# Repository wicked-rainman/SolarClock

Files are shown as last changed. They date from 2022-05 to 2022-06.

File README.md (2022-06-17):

# SolarClock
<p align="center">
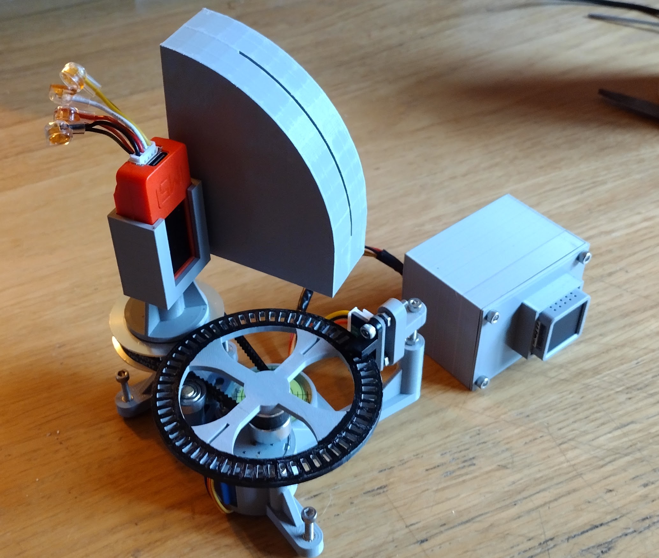
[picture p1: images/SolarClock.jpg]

</p>
 
This project shouldn't be confused with a plan to design a clock powered by solar energy. That's not what this is about. Instead, it represents an academic attempt at calculating the time based on the position of the sun in the sky.

Yes, you could look at your watch, listen for the pips on the radio or even glance at your mobile phone - but this isn't a move to try and replace those reliable sources. It's more about trying to observe the local environment and making calculations around what can be seen.   

I can't pretend when this is finished it will have much value - it's more of a nonsense machine bred out of boredom. Regardless, I do think it will be interesting to see how accurately time can be calculated using a bunch of cheap electronics and some 3D printed tat.
 
There will probably end up being just two main components in all of this:

- A "Stepper motor server" being driven via an M5Atom-matrix, although any esp32/Arduino type platform would do. I chose the Matrix because I had one spare and could make use of the LED array for added glitz.
- A "Stepper client" that will read light values and instruct the server how far to rotate after each reading. This component is based round an M5Stick because it's got a built in battery that helps negate the need for trailing wires being dragged round by the rotating platform.

When I started out on this venture, I tried using an I2C based compass (LSM303) for azimuth alignment. Like any "sundial", you have to know which way is north. The LSM303 claimed a 0.1 degree resolution, but after some failed tests and a bit of reading I discovered that although the resolution is good, accuracy is +-5 degrees. Given that the earth rotates through roughly 15 degrees in an hour, It just wouldn't provide the accuracy I'm looking for. So, in the end I went back to the drawing board and came up with a timing disk design. The main drawback of this approach is you need to manually ensure the light sensing unit is facing true north whenever you press the inevitable "go" button. This dosen't satisfy me as a solution, but for now it will have to do.

## North
Finding true north is problematic. You could use a normal magnetic compass and deal with the offset, but from what research I've done so far this seems a little vague (Magnetic north is always on the move). I'm still considering adding some form of gnomon to the rotator base so it can be aligned (after performing solar observations), but that loses the semi-instant gratification of just pushing a button I've also been considering a gyro, but that leads towards the chicken and egg situation of still not actually knowing where true north is in the first place. I've read some of the physics and I'm well aware that a gyro can achieve this because it's affected by the rotation of the earth. Such a gyro is really expensive and I don't think I'm capable of constructing one of my own. For now I'm going to carry on testing commercially availble magnetometers to see if there's something better than the LSM303. Watch this space.

<b><i>Updates:</i></b>

- 12th June 2022. Finished an evaluation of another magnetometer, the BMM150. I chose this one to test because it's actually sold as a viable and accurate compass. In my usecase, this still proved to be unreliable. I have a suspicion that even after calibration the environment is too electrically noisy. I'm currently planning to drop the idea of using any of these i2c devices, although I might change my mind at a later stage. I'm now thinking there may need to be a physically separate component to this project in order to perform the initial allignment. 

- Going back to the drawing board again, I've since discovered that for my geographic area, the magnetic declination is currently 0.12 mins, i.e. 0.2 degrees. I don't know what the annual variation is, but I'm heading towards the more simple concept of just drawing an accurate east/west line. I'll position the rotating head at a right angles to this before I start. I can draw the rhumb line "offline" so there is no equipment interference and for now, just accept the accuracy of a normal bearing compass. 

<p align="center">
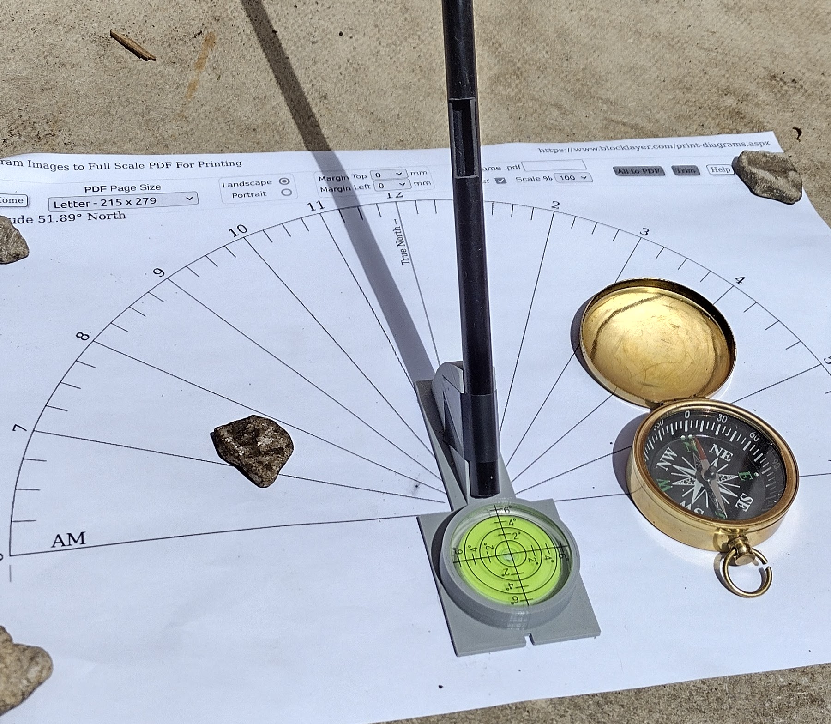
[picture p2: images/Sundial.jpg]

</p>

- Performed some cross check tests in the back garden to correlate the whole magnetic north/true north solar time theory. I don't know why, but I'm surprised at just how accurate the results are. This gives me some confidence that I should be able to correctly calculate the time within at least a 15 min window. Clearly, my earlier views were just plain wrong! 

## The Components - Stepper motor server

- M5Atom matrix (*The Stepper motor WiFi server platform*)
- 28BYJ-48 5V stepper motor with ULN2003 driver
- Infra-red photo interrupter sensor
- Round button-type spirit level
- GT2 200 tooth belt, 20 and 60 tooth belt pulley
- 5mm brass rod
- Pulley tensioner bearing (*14mm od, 5mm id*)
- 3d M3 inserts (12)
- Assortment of M3 machine screws
- 3D printed components - as stored in the STL directory
- (Maybe a desire to wait for a day when it isn't raining and you can see the sun?)

## Stepper client

- M5Stickc (I'm using the PLUS variant)
- BH1750 light sensor (*in I2C mode*)
- Some (as yet to be decided) magnetometer

## Notes:

- This is a work in progress !!
- In the UK, the sun can rise at 50 degrees east and set at 310 west (this is it's local maximum azimuth boundary). The stepper motor client has therefore been set to only sweep between these angles, one degree (but 30 odd stepper motor half steps) at a time. In theory, this should allow for a resolution of about 2 mins, but I doubt that such accuracy is achievable.
- The HM1750 light sensor on the client has been set up so it only has a 1mm vertical view of the sky (from an elevation of 10 degrees through to 65 - the minimum and maximum throughout the year. The container box for the sensor looks odd, but there is a reason behind this. Obviously, the closer the sensor is to the apeture, the more of the sky can be seen (Think peeping through a keyhole). Given that the stepper platform is being advanced by one degree at a time, it seemed to make sense for the sensor view to be similarly restricted. I have no idea if this is the right decision, but it's only another 3d print away from being correctable!. In theory, 360mm circle circumference means a 57.3mm viewing radius - thus the odd size and shape.  
- The pulley ratio on the stepper server is 3:1 - I.E, the stepper motor has to rotate three times in order for the output pulley (the base) to rotate once. The timing disc has 60 slots in it - giving 120 pulses (60 on and 60 off) per revolution. 120 x 3 = 360. The stepper motor seems to take 40 odd half steps to clear a slot and roughly 20 to clear each space. Part of the reason for this difference is that the top edges of the space segments are narrower than the bottom. Using Tinkercad I couldn't see a way round this issue - but I don't believe it's going to matter that much. If it does become problematic the difference can be catered for in the code.  

<p align="center">
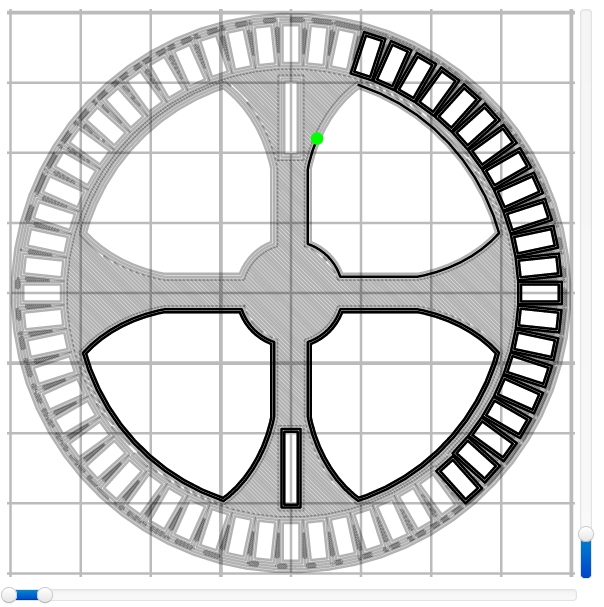
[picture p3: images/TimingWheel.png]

</p>
 <p align="center">
 <b>The mark and space variation</b>
</p>

- The Stepper client and server communicate over WiFi using UDP. What with the M5Stick's built in battery this removes any need for wiring between the stepper base and rotator. I decided on UDP rather than TCP to reduce cpu loads. Communication re-tries are seen, but the current code seems to address this shortfall.

```mermaid
sequenceDiagram
    participant StepperClient
    participant StepperServer
    participant UDPBroadcast
    Note left of StepperClient: Press M5Stick<BR/> Button A.
    StepperClient->>StepperServer: Rotate request for 50 North, UDP port 5001
    StepperServer->>StepperClient: Ack on UDP port 5002, now pointing 50 North
    activate StepperClient
    Note left of StepperClient: Repeat in 1 degree<br>increments until<BR/>310 degrees reached.
    StepperClient->>StepperServer: Rotate request for 1 degree clockwiseff (UDP port 5001)
    StepperServer->>StepperClient: Rotate 1 degree Ack, (UDP 5002)
    StepperClient->>UDPBroadcast: Lux and Azimuth values (UDP port 5003)
    deactivate StepperClient
    Note left of StepperClient: Sweep completed
    StepperClient->>UDPBroadcast: Azimuth with max Lux result
```
- As already highlighted, the apeture box face must be pointing towards true north. When the front button on the M5Stick is pressed, degree position zero is assumed. The rotate to the 50 degrees start point (after a short pause) is then initiated. After that, the "1 degree at a time" step scan for the brightest bearing takes place.

- At some stage, it could be that the HM1750 sensor will need to be vertically rotated from 10 to 65 degrees during the scan. Doing this might provide better resolution as to where the sun really is - I'll only know after doing some tests.

- [Tinkercad](https://www.tinkercad.com/things/aQJdY34zP4q) files available here if you want to modify the design

# Interim results

On the 15th June 2022 I managed to get a set of tests done using an apeture slit width of just over 1mm. It was a bright sunny day with a clear sky, so it seemed an ideal time. After manually aligning the sensor with true north (by sight), I performed the first test at 09:23AM. According to the tables I'm using as a reference, the sun should have an azimuth of 100.79 degrees and then 101.9 at 09:25AM. During this first test, the sensor returned a value of 54612 for bearing 100 and 51554 for 101. All other light readings had low 3 digits values. 
<p align="center">
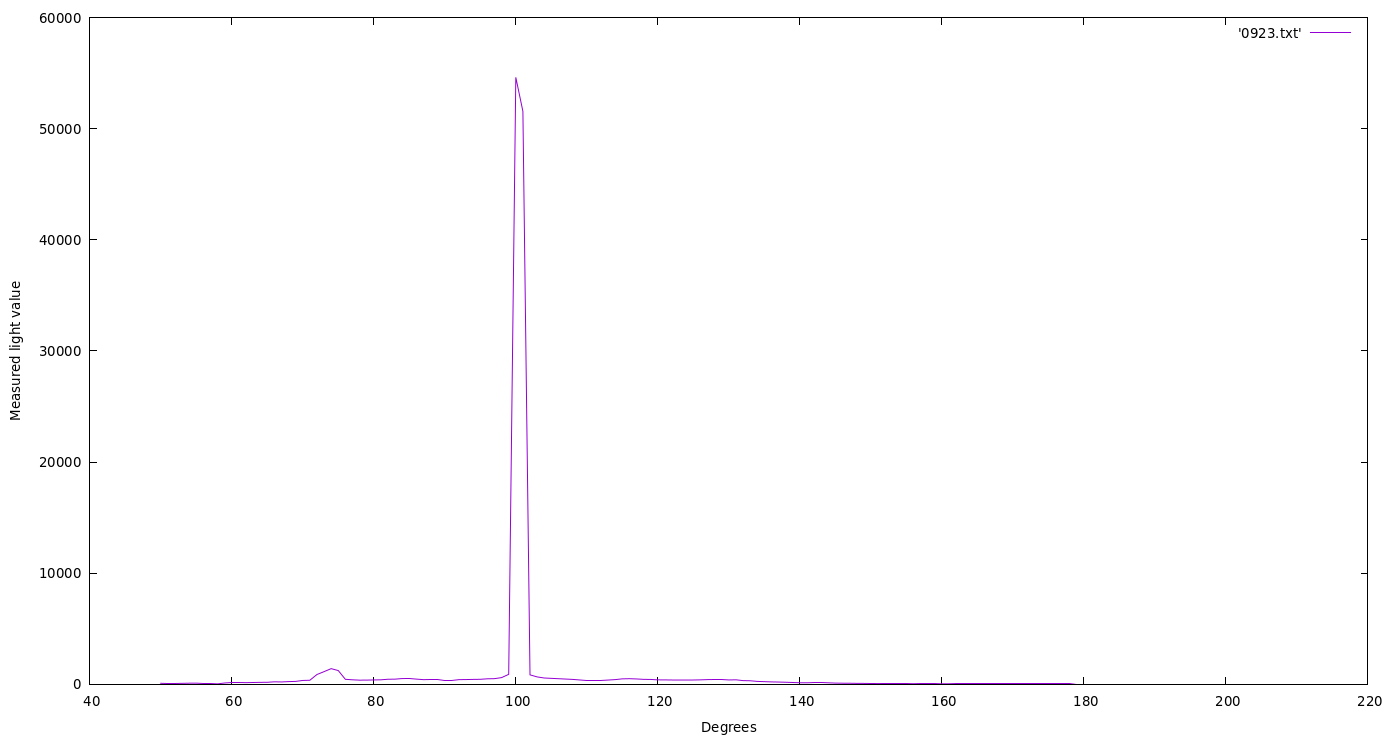
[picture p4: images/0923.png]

</p>

The second test was run at 09:26. Again, the tables show an azimuth of 101.9 degrees and 103.2 for 09:30AM. For bearing 101 I got a value of 3613. For 102 the value was 18735 and for 103, 13504. 
<p align="center">
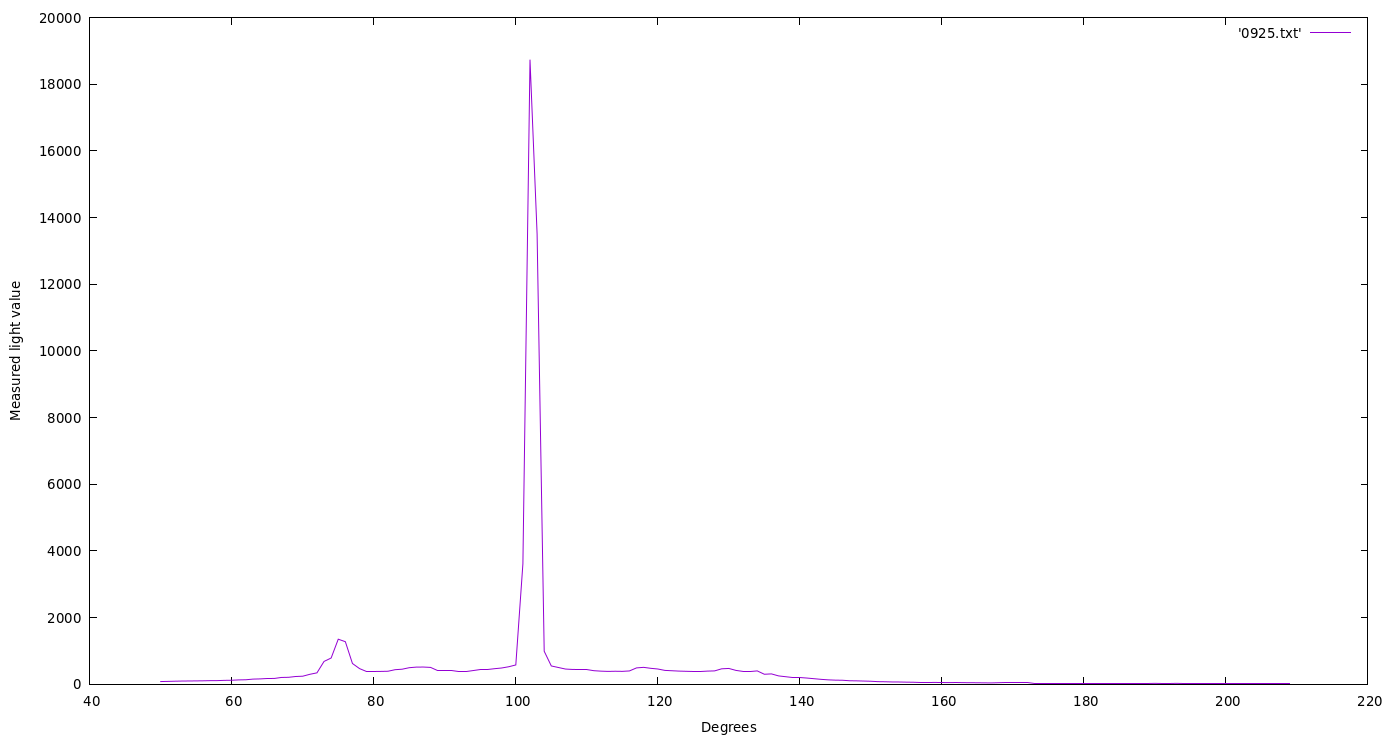
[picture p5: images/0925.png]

</p>
Here, as you can see, the highest bearing was 102. It's interesting (to me) that I got a high'ish value for bearing 101, but the light peak is still very obvious. I'm very pleased with the results because with these short tests I seem to be well within a +/- 5 mins tolerance. That's better than I initially expected. Clearly I will have to embed some lookup table in the code, but that's easy. For now I'm going to focus on trying to improve the accuracy and mark this down as prototype version 1. 

[Here's ](https://youtube.com/shorts/W4BCCfyBn9M) a really dull video of it running during the test. 

To be continued...

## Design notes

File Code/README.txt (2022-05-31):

Code for Stepper motor server and client

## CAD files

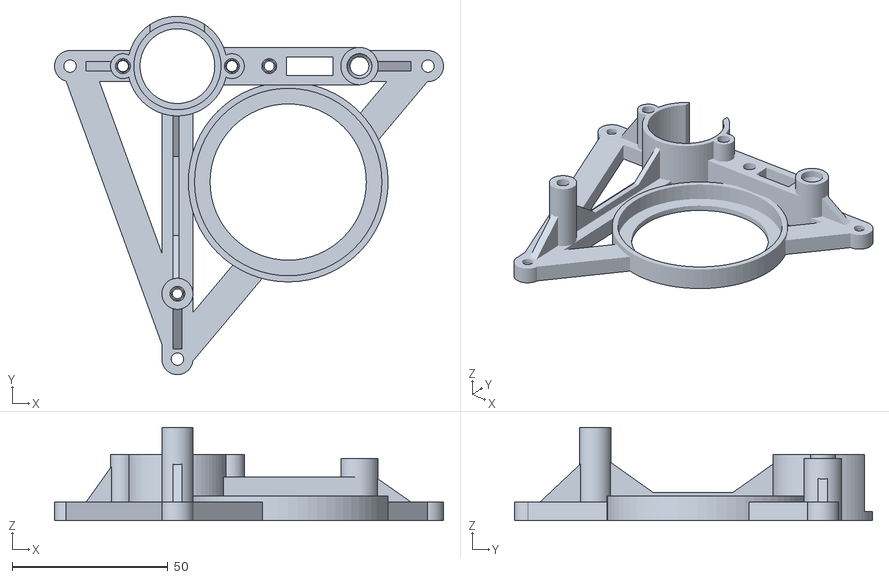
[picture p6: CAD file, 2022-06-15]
STL/RotatorBase-V0.2.stl
125.0 x 115.2 x 30.0

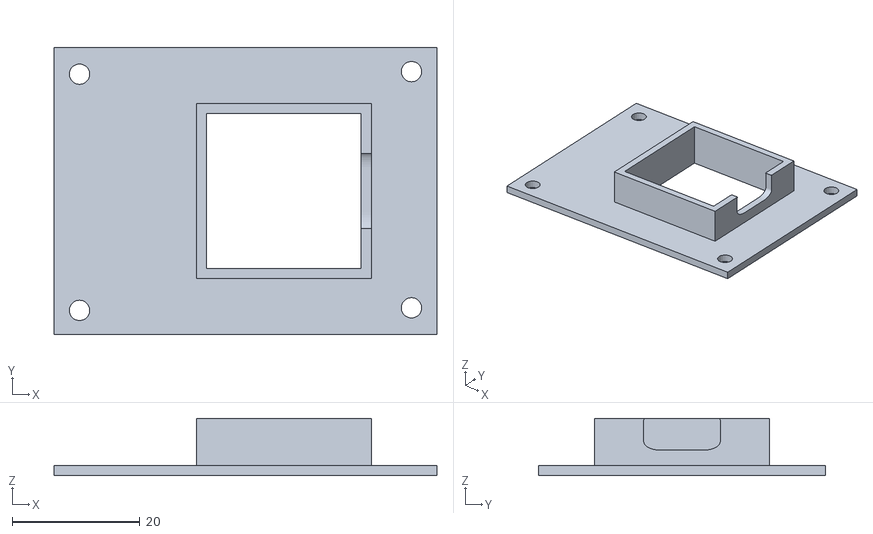
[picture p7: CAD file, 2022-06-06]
STL/ControllerBoxLid.stl
60.0 x 45.0 x 9.00

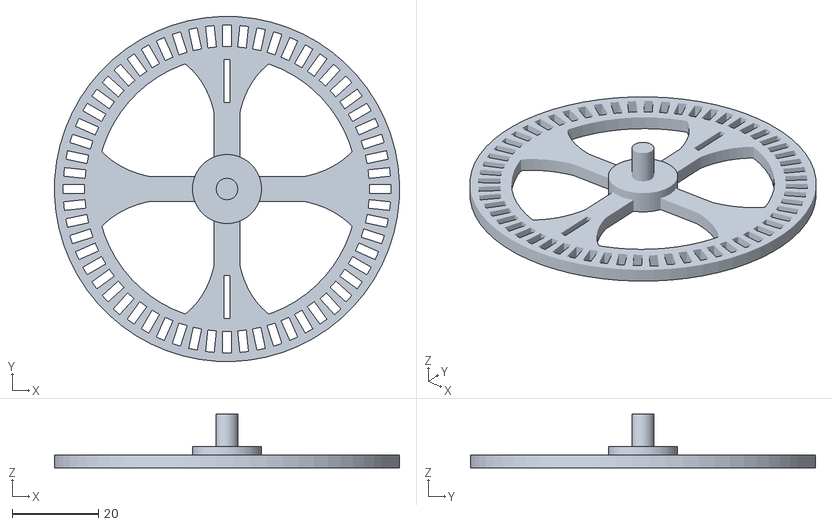
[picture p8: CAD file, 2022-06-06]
STL/TimingRing.stl
80.0 x 80.0 x 12.5

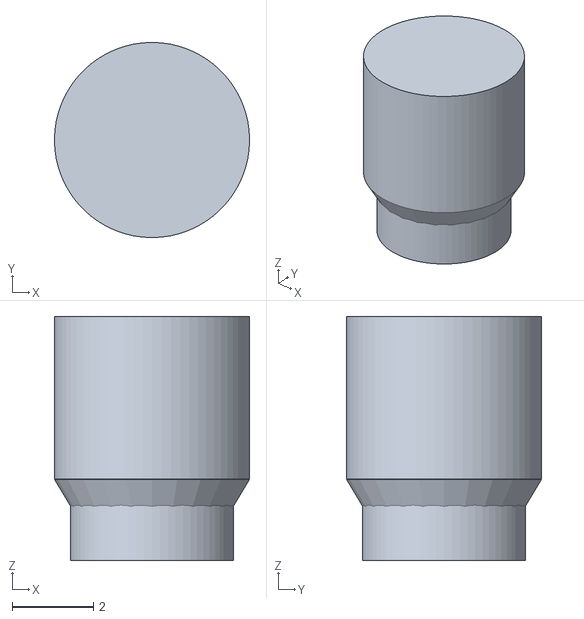
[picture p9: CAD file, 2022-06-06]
STL/M3Insert.stl
4.80 x 4.80 x 6.00

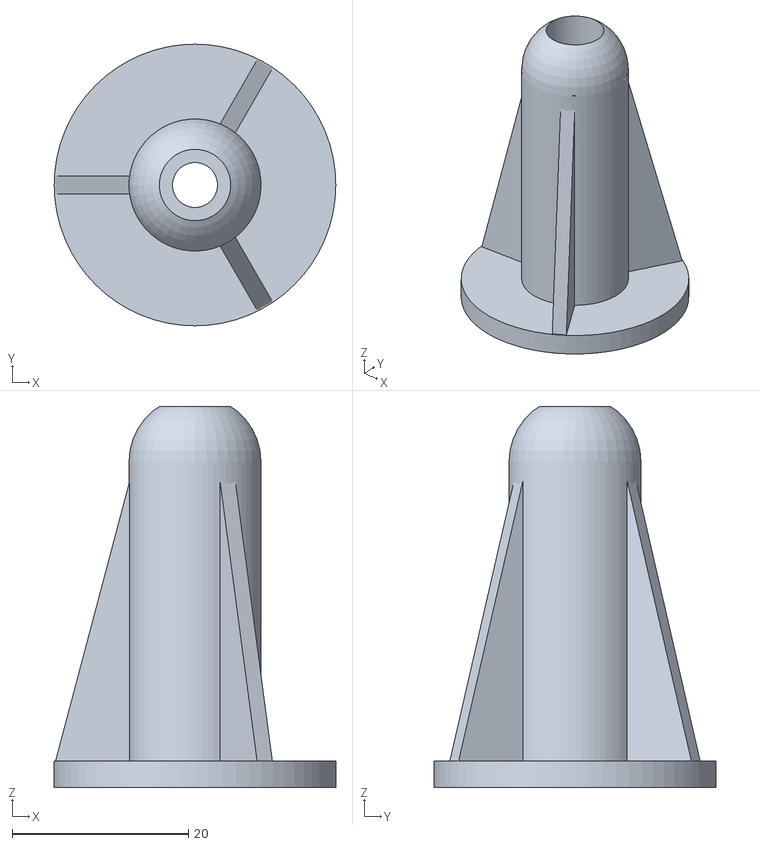
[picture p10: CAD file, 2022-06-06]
STL/Standoff.stl
32.0 x 32.0 x 43.3

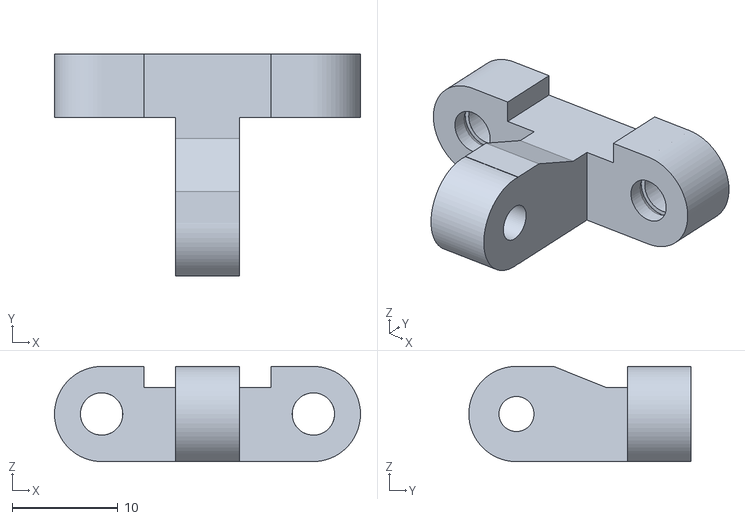
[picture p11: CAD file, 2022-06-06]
STL/SlotSensorCarrier.stl
28.9 x 21.0 x 9.00

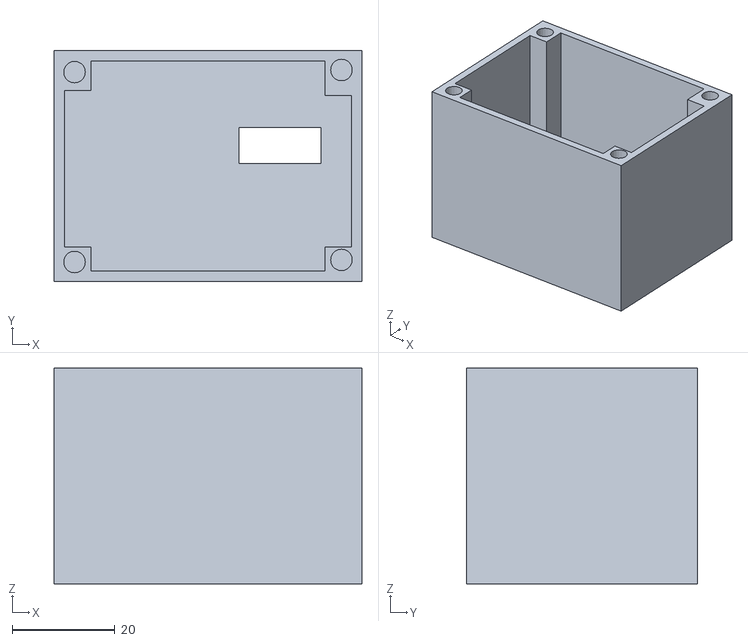
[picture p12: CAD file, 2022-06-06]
STL/ControllerBox.stl
60.0 x 45.0 x 42.0

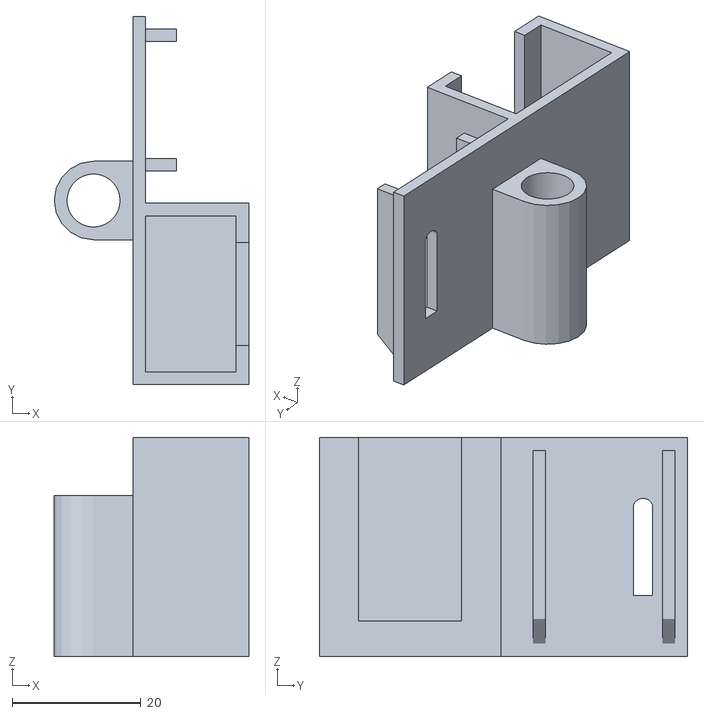
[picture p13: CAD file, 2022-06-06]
STL/Carrier.stl
30.2 x 57.2 x 34.0

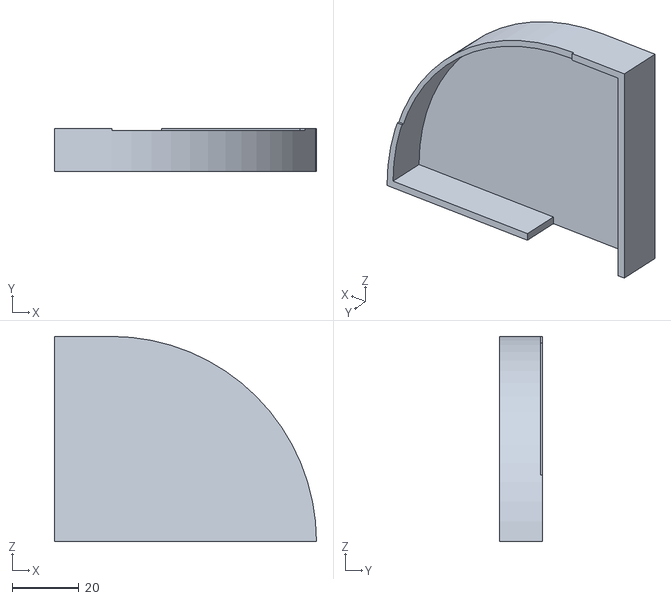
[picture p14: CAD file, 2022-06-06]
STL/ApetureBoxSide2.stl
78.4 x 13.0 x 61.4

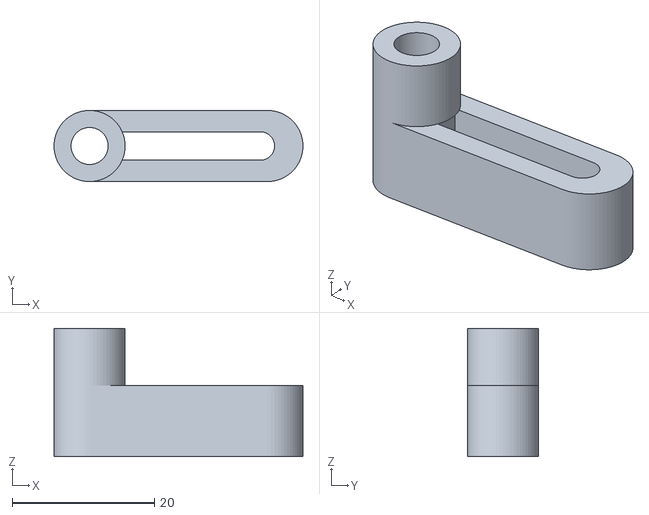
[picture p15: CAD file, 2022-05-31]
STL/BeltTensionerv01.stl
35.0 x 10.0 x 18.0

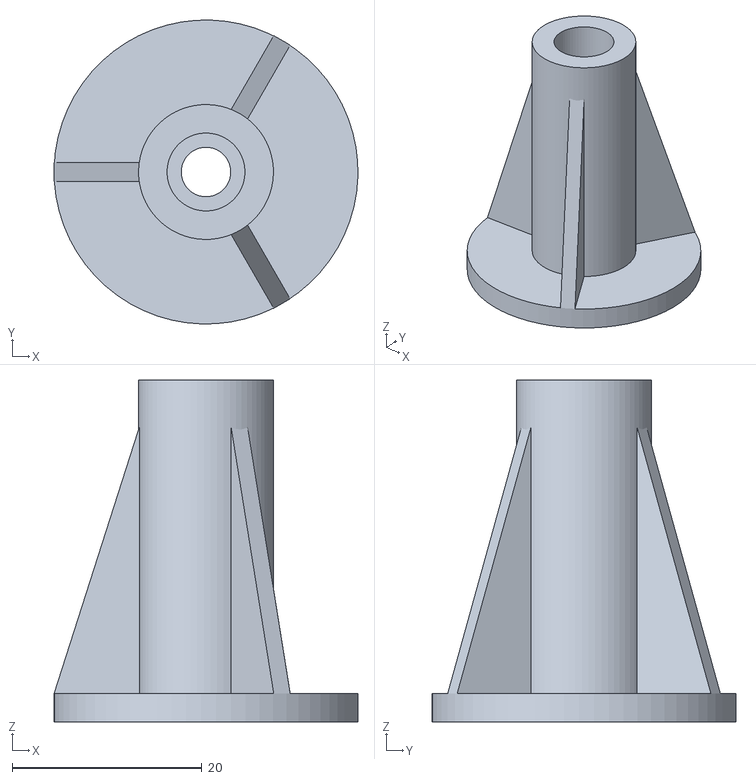
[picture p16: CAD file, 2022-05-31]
STL/RotatorShaftBase.stl
32.0 x 32.0 x 36.0

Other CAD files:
STL/ApetureBoxSide1.stl

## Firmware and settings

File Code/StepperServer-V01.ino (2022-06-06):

#include <M5Atom.h>
#include <WiFi.h>
#include <WiFiUdp.h>
#define SPIN_REQUEST_PORT 5001
#define SPIN_REPLY_PORT 5002

#define ROTATION_DELAY 8                 //Defines low pulse duration after stepper coil stimulation
#define HALFSTEP_PULSE_LEN 4             //Defines high pulse duration when stimulating stepper coil - Halfstep
#define CLOCKWISE true                   //Stepper rotation direction 
#define ANTICLOCKWISE false              //Stepper rotation direction

#define In1 33
#define In2 23
#define In3 19
#define In4 22
#define Photo 25
static int StepPosition = 0;
static int Bearing;
IPAddress SendIP(192, 168, 68, 255);
const char* ssid = "xxxxx";
const char* pass = "xxxxx";
WiFiUDP udpRX, udpTX;

void setup() {
  M5.begin(true, true, true);
  pinMode(In1, OUTPUT); digitalWrite(In1, LOW);
  pinMode(In2, OUTPUT); digitalWrite(In2, LOW);
  pinMode(In3, OUTPUT); digitalWrite(In3, LOW);
  pinMode(In4, OUTPUT); digitalWrite(In4, LOW);
  pinMode(Photo, INPUT);
  Serial.begin(115200);
  WiFi.begin(ssid, pass);
  while (WiFi.status() != WL_CONNECTED) {
    M5.dis.drawpix(4, 0xff0000);
    delay(100);
    M5.dis.clear();
    delay(100);
  }
  Bearing = 0;
  StepPosition = 0;
  M5.dis.drawpix(4, 0x00ff00);
  udpRX.begin(SPIN_REQUEST_PORT);
  udpTX.begin(SPIN_REPLY_PORT);
}

void loop() {
  int packetSize = 0;
  int payloadSize = 0;
  char packet[20];
  boolean SpinDirection;
  char StrBearing[50];
  int WantedBearing = 0;

  packetSize = udpRX.parsePacket();
  if (packetSize) {
    memset(packet, 0, 20);
    payloadSize = udpRX.read(packet, 10);
    if (payloadSize == 3) {
      M5.dis.drawpix(9, 0xff0000);
      WantedBearing = atoi(packet);
      if (WantedBearing > Bearing) {
        Serial.printf("Bearing=%d. Wanted=%d. Rotating clockwise\n", Bearing, WantedBearing);
        while (Bearing != WantedBearing) {
          RotateBase(CLOCKWISE);
          Bearing++;
        }
      }
      if (WantedBearing < Bearing) {
        Serial.printf("Bearing=%d. Wanted=%d. Rotating anti-clockwise\n", Bearing, WantedBearing);
        while (Bearing != WantedBearing) {
          RotateBase(ANTICLOCKWISE);
          Bearing--;
        }
      }
      M5.dis.drawpix(9, 0x000000);
    }
    else {
      Serial.printf("Invalid packet (%d) \"%s\"\n", payloadSize, packet);
    }
    Reply();
  }
}

void Reply() {
  char replystr[10];
  memset(replystr, 0, 10);
  snprintf(replystr, 5, "%3d", Bearing);
  udpTX.beginPacket(SendIP, SPIN_REPLY_PORT);
  udpTX.print(replystr);
  udpTX.endPacket();
}

void TogglePixels(int colour, int led1, int led2, int led3, int led4, int led5) {
  static int islit = 1;
  switch (islit) {
    case 1 : {
        M5.dis.drawpix(led5, 0xff000000);
        M5.dis.drawpix(led1, colour);
        break;
      }
    case 2 : {
        M5.dis.drawpix(led1, 0xff000000);
        M5.dis.drawpix(led2, colour);
        break;
      }
    case 3 : {
        M5.dis.drawpix(led2, 0xff000000);
        M5.dis.drawpix(led3, colour);
        break;
      }
    case 4 : {
        M5.dis.drawpix(led3, 0x000000);
        M5.dis.drawpix(led4, colour);
        break;
      }
    case 5 : {
        M5.dis.drawpix(led4, 0x000000);
        M5.dis.drawpix(led5, colour);
      }
  }
  if (islit == 5) islit = 1;
  else islit++;
}


void RotateBase(boolean RotateDirection) {
  int k;
  boolean state;
  state = (boolean) digitalRead(Photo);
  k = 0;
  while ((boolean) digitalRead(Photo) == state) {
    k++;
    if (RotateDirection == true) {
      TogglePixels(0x00ff00, 0, 5, 10, 15, 20);
      StepPosition--;
      if (StepPosition < 1) StepPosition = 8;
    }
    else {
      StepPosition++;
      TogglePixels(0x0000ff, 0, 5, 10, 15, 20);
      if (StepPosition > 8) StepPosition = 1;
    }
    switch (StepPosition) {
      case 1: {
          digitalWrite(In1, HIGH);
          delay(HALFSTEP_PULSE_LEN);
          digitalWrite(In1, LOW);
          delay(ROTATION_DELAY);
          break;
        }
      case 2: {
          digitalWrite(In1, HIGH);
          digitalWrite(In2, HIGH);
          delay(HALFSTEP_PULSE_LEN);
          digitalWrite(In1, LOW);
          digitalWrite(In2, LOW);
          delay(ROTATION_DELAY);
          break;
        }
      case 3: {
          digitalWrite(In2, HIGH);
          delay(HALFSTEP_PULSE_LEN);
          digitalWrite(In2, LOW);
          delay(ROTATION_DELAY);
          break;
        }
      case 4: {
          digitalWrite(In2, HIGH);
          digitalWrite(In3, HIGH);
          delay(HALFSTEP_PULSE_LEN);
          digitalWrite(In2, LOW);
          digitalWrite(In3, LOW);
          delay(ROTATION_DELAY);
          break;
        }
      case 5: {
          digitalWrite(In3, HIGH);
          delay(HALFSTEP_PULSE_LEN);
          digitalWrite(In3, LOW);
          delay(ROTATION_DELAY);
          break;
        }
      case 6: {
          digitalWrite(In3, HIGH);
          digitalWrite(In4, HIGH);
          delay(HALFSTEP_PULSE_LEN);
          digitalWrite(In3, LOW);
          digitalWrite(In4, LOW);
          delay(ROTATION_DELAY);
          break;
        }
      case 7: {
          digitalWrite(In4, HIGH);
          delay(HALFSTEP_PULSE_LEN);
          digitalWrite(In4, LOW);
          delay(ROTATION_DELAY);
          break;
        }
      case 8: {
          digitalWrite(In4, HIGH);
          digitalWrite(In1, HIGH);
          delay(HALFSTEP_PULSE_LEN);
          digitalWrite(In4, LOW);
          digitalWrite(In1, LOW);
          delay(ROTATION_DELAY);
          break;
        }
      default : {
          Serial.println("I slept with your Mom");
          break;
        }
    }
  }
}

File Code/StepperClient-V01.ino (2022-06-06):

#include <M5StickCPlus.h>
#include <WiFi.h>
#include <WiFiUdp.h>
#include <Wire.h>
#include <BH1750.h>

#define DATA_PORT 5003
#define ROTATE_REQUEST_PORT 5001
#define ROTATE_REPLY_PORT 5002
BH1750 lightMeter;
IPAddress SendIP(192, 168, 68, 255);
const char* ssid = "xxxxx";
const char* pass = "xxxxx";
WiFiUDP udpDataOut, udpRotateRequest, udpRotateReply;
float Lux;
int LuxInt;
static int Bearing;

void setup() {
  M5.begin(true, true, true);
  Serial.begin(115200);
  M5.Lcd.setRotation(2);
  M5.Lcd.setTextSize(3);
  WiFi.begin(ssid, pass);
  while (WiFi.status() != WL_CONNECTED) {
    delay(1000);
  }
  Wire.begin();
  lightMeter.begin();
  udpDataOut.begin(DATA_PORT);
  udpRotateRequest.begin(ROTATE_REQUEST_PORT);
  udpRotateReply.begin(ROTATE_REPLY_PORT);
  Bearing = 0;
  M5.Lcd.fillScreen(BLACK);
  M5.Lcd.setCursor(1, 0);
  M5.Lcd.print("Ready");
}

void loop() {

  char payload[40];
  int k;
  int brightBearing ;
  float maxLux;
  M5.update();
  if (M5.BtnA.wasReleased()) {
    brightBearing = 0; maxLux = 0.0;
    M5.Lcd.fillScreen(RED);
    RequestRotate(49, 30);
    M5.Lcd.fillScreen(BLACK);
    for (Bearing = 50; Bearing < 210; Bearing++) {
      Bearing = RequestRotate(Bearing, 3);
      Lux = lightMeter.readLightLevel();
      if (Lux > maxLux) {
        maxLux = Lux;
        brightBearing = Bearing;
      }
      LuxInt = round(Lux);
      M5.Lcd.fillScreen(BLACK);
      M5.Lcd.setCursor(0, 0);
      M5.Lcd.printf("\n%d\n\n%d\n", Bearing, LuxInt);
      Serial.printf("%d,%f\n", Bearing, Lux);
      sendData(Bearing, Lux);
    }
      M5.Lcd.fillScreen(BLACK);
      M5.Lcd.setCursor(0, 0);
      M5.Lcd.print("Done");
      M5.Lcd.setCursor(0, 30);
      M5.Lcd.print(brightBearing);
      Serial.printf("Lightest bearing = %d degrees (Lux value was %f)\n", brightBearing, maxLux);
    }
  }

  void sendData(int compassval, float Lux) {
    char payload[40];
    memset(payload, 0, 40);
    snprintf(payload, 40, "%d,%f\n", compassval, Lux);
    udpDataOut.beginPacket(SendIP, DATA_PORT);
    udpDataOut.print(payload);
    udpDataOut.endPacket();
  }


  int RequestRotate(int bearing, int MaxWaitTime) {
    char rotateReply[20];
    int payloadSize = 0, packetSize = 0, reply = 0;;
    int waitTime = 0;

    sendRequest(bearing);
    //Now wait for a reply to say the servo server has done the job
    while (reply != bearing) {
      packetSize = udpRotateReply.parsePacket();
      if (packetSize) {
        memset(rotateReply, 0, 20);
        payloadSize = udpRotateReply.read(rotateReply, 20);
        if (payloadSize == 3) reply = atoi(rotateReply);
        else sendRequest(bearing);
      }
      delay(1);
      if (waitTime++ >= MaxWaitTime * 1000) {
        Serial.printf("#Repeating request for bearing %d\n", bearing);
        sendRequest(bearing);
        waitTime = 0;
      }
    }
    return bearing;
  }

  void sendRequest(int bearing) {
    char bearingStr[10];
    memset(bearingStr, 0, 10);
    snprintf(bearingStr, 5, "%3d", bearing);
    udpRotateRequest.beginPacket(SendIP, ROTATE_REQUEST_PORT);
    udpRotateRequest.print(bearingStr);
    udpRotateRequest.endPacket();
  }
